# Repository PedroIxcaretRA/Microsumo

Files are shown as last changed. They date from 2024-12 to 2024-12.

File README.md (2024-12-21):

# Microsumo
Diseño, Programación y PCB para realizar un sumo clase 100gr (Microsumo)

## Tabla de Contenidos
1. [Descripción](#descripción)
2. [PCB](#pcb)
3. [Diseño](#diseño)
4. [Código](#código)

## Descripción
En el mundo de la robótica móvil, puede resultar un poco complicado encontrar información para desarrollar un prototipo en alguna de las diversas categorías existentes, como lo son sumo, seguidor de línea, robot de combate, drones autónomos, micromouse, entre otras. Si bien es posible encontrar cierta información de algunas categorías en repositorios de GitHub, videos de YouTube o artículos, esta puede estar en cualquier otro idioma, por lo que sea difícil su interpretación.

Por ello, en este repositorio, el objetivo es compartir todo lo aprendido en la categoría sumo, específicamente en la clase 100 gramos (micro). Esperamos que esta información sea completa y útil para tus proyectos, o al menos te brinde una idea clara de lo que implica esta categoría.

## PCB

En esta sección se comparte un Gerber perteneciente a una PCB realizada por nosotros. Al igual que se da el esquemático y una breve explicación para realizar una.

## Diseño

Se comparten archivos e ideas que hemos utilizado y algunas recomendaciones que podrían ser de ayuda.

## Código

En esta sección se comparte un código ejemplo y se da una breve explicación. 

Autores:
[MOCteam](https://www.instagram.com/mocteam17/)

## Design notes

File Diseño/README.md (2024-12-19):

# Diseño y Ensamble

El diseño del prototipo, al igual que el diseño de la PCB o la programación, evoluciona con el tiempo. Se prueba una cosa y otra, y aunque al principio puede que no se tenga un buen prototipo (o si), después de dos o tres competencias podrías identificar aspectos que necesiten cambios. Nuevas ideas y mejoras siempre surgen. Por eso, en esta parte del repositorio se presentará una idea general del diseño mecánico del robot, así como del ensamble del prototipo. Como en todo el repositorio, puedes seguir estos pasos al pie de la letra o adaptarlos según tus necesidades.

***Aunque dice "Diseño", y lo más probable es que se piense que aquí se enseñará a cómo diseñar un microsumo, la realidad es que con los archivos que se están compartiendo ya se puede tener una idea clara de cómo hacerlo. Por lo tanto, esta sección se centrará más en consejos prácticos y el ensamblaje del prototipo.***

## Tabla de Contenidos
1. [Descripción](#descripción)
2. [Base latón](#base-latón)
   - [Paredes](#paredes)
     - [Ensamblaje](#ensamblaje)
   - [Base sensores](#base-sensores)
4. [PLA](#pla)

## Descripción

El archivo base_microsumo_pro.rar contiene una base diseñada en SolidWorks (versión 2019), destinada a ser fabricada en latón. Puede ser enviada a maquilar en JLCPCB, PCBWAY, o cualquier otro lugar. Este archivo es totalmente modificable y lo puedes ajustar según tus necesidades.

No es fundamental usar una base de latón en un microsumo, versiones anteriores que se han realizado, el chasis del robot ha sido completamente de PLA con peso muerto (plomo), ha funcionado bastante bien, así que, si se prefiere usar PLA y plomo es una opción bastante viable, en el archivo Microsumo_v10.rar es una idea de lo que se usaba. Igual es totalmente modificable.

***Tip***
- El ángulo donde se coloca la navaja generalmente varía entre 20° y 30° de inclinación. Como recomendación, se sugiere usar un ángulo de 25°.

## Base latón

Una vez que se tiene la base de latón en proceso de fabricación o en su posesión, ya sea que se haya mandado a fabricar la opción presentada, modificado el diseño existente o incluso creado una propia, se procederá a diseñar el chasis del prototipo. 

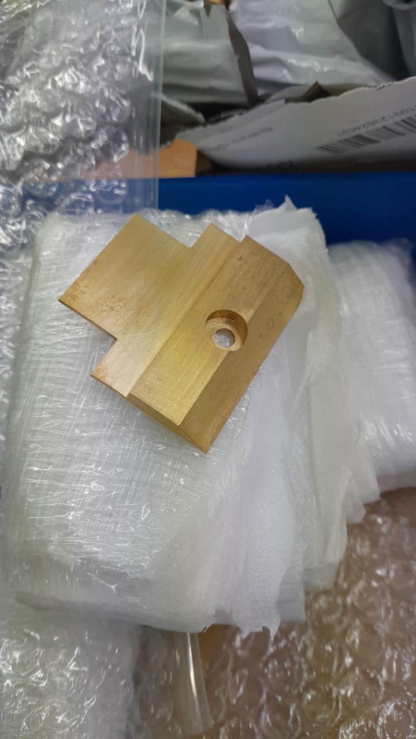
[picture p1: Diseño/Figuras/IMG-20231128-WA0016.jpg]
Baselaton


Para esto, se darán dos opciones que hemos utilizado, las cuales llamaremos *Paredes* y *Base Sensores*. 
- Paredes: Como su nombre lo indica, se tendrán las paredes laterales y trasera, fabricadas de PLA o cualquier otro filamento.
- Base Sensores: consiste en una pequeña base donde se colocaran los sensores y la tapa frontal, también fabricada de PLA.

En ambas opciones, la tapa frontal será construida de una herramienta conocida como [cuña](https://www.brochasexito.com.mx/productos/Accesorios/Cunas-Exito-de-Acero), esta herramienta se puede conseguir en COMEX (Mexico).

### Paredes

Se diseñará en la parte de arriba de la base algo como lo siguiente.

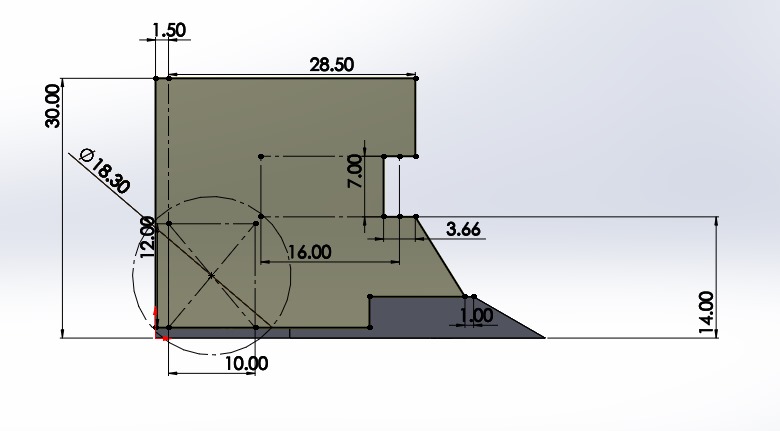
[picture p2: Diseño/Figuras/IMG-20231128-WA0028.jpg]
Paredes_moc


Las medidas dependerán de los sensores, batería(s), llantas y motores que se estén utilizando. En el ejemplo anterior se emplearon dos baterías de litio de 3.7V y 140mAh (RADOX), tres sensores de proximidad IR Pololu 38kHz de ganancia fija, dos micromotorreductores N20 de relación 30:1, un sensor QTR (de autoría propia), además de un par de rines y llantas.

Aunque se pueden hacer mejoras, por ejemplo:
- La tapa trasera podría reducirse a 1 mm o 0.5 mm.
- La medida de 28.5 mm podría ajustarse a 25 mm.
- La altura de 30 mm podría reducirse a 25 mm o 27 mm.

Estos cambios modificarían ciertas partes del diseño, pero consideramos que quedarían a la perfección. Es cuestión de experimentar con lo que se tiene y ajustar según las necesidades.

#### Ensamblaje

Se puede pintar la base o colocar una pegatina, ya sea en un acabado totalmente negro, brillante o mate o tipo fibra de carbono. Esto dependerá del gusto de cada persona.

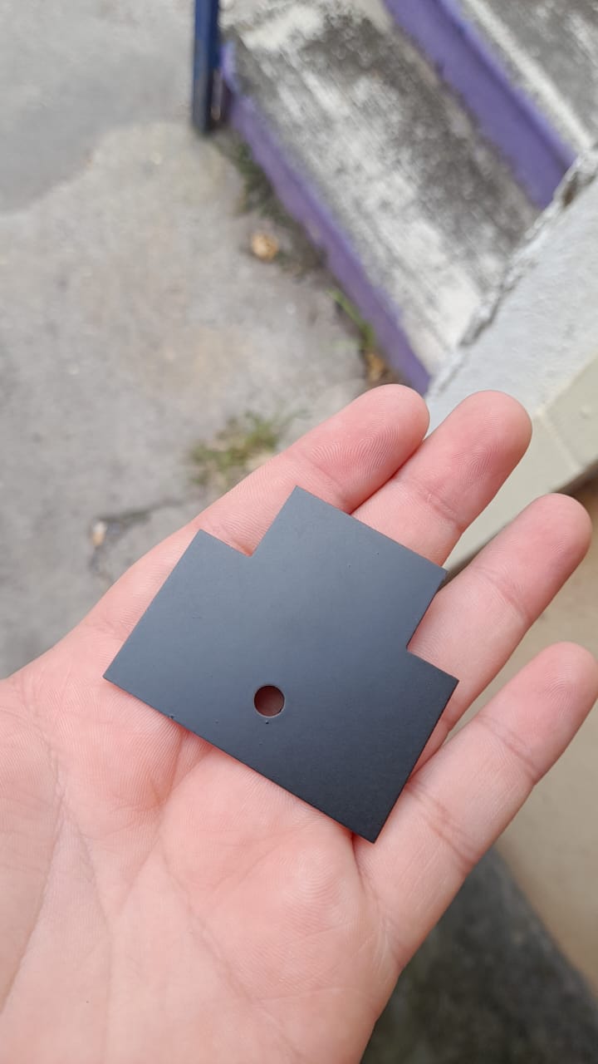
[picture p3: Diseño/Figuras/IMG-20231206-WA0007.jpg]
Basepint


Una vez que se tienen las impresiones en 3D de las paredes, estas se fijan a la base de latón utilizando Kola-Loka. Colóquese pared por pared, con calma, para tener un mejor resultado. El resultado final debería verse de la siguiente manera.

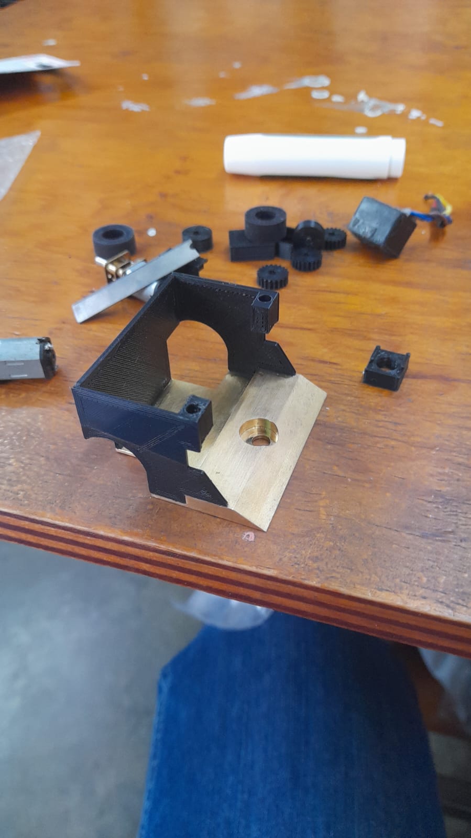
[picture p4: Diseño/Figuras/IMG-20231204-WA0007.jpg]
BasePar


A partir de aquí, el ensamblaje será el mismo si se utilizan motores N20 rectos, ya que existen diferentes modelos. ¿Qué significa que será el mismo? Justamente eso: sin importar cuál opción se utilice (Paredes o Base Sensores, con base de latón o PLA), la forma en la que se colocarán los motores y cómo se transmitirá la potencia será igual para todas las configuraciones. Por lo tanto, se explicará el proceso con el máximo detalle.

La idea es colocar los motores como se muestra en la figura de abajo. 
Para fijar los motores a la base, se utiliza Kola-Loka. Como sugerencia adicional, se podría agregar un poco de bicarbonato a la mezcla. Esto genera una sustancia más fuerte y resistente.

***Tip***

- Supondremos que ya se cuentan con las llantas. Una sugerencia importante que debes seguir al pie de la letra es no fijar los motores al 100%. Utiliza únicamente la cantidad necesaria de Kola-Loka para que los motores queden semifijos y no se muevan.
Una vez que estén semifijados, coloca las llantas y verifica que no haya desnivel utilizando un espejo (por el reverso del mismo). Es fundamental asegurarse de que la parte donde se colocará la navaja quede recargada de manera uniforme sobre la superficie. Esto para que cuando se coloque la navaja no se tenga un lado alzado.

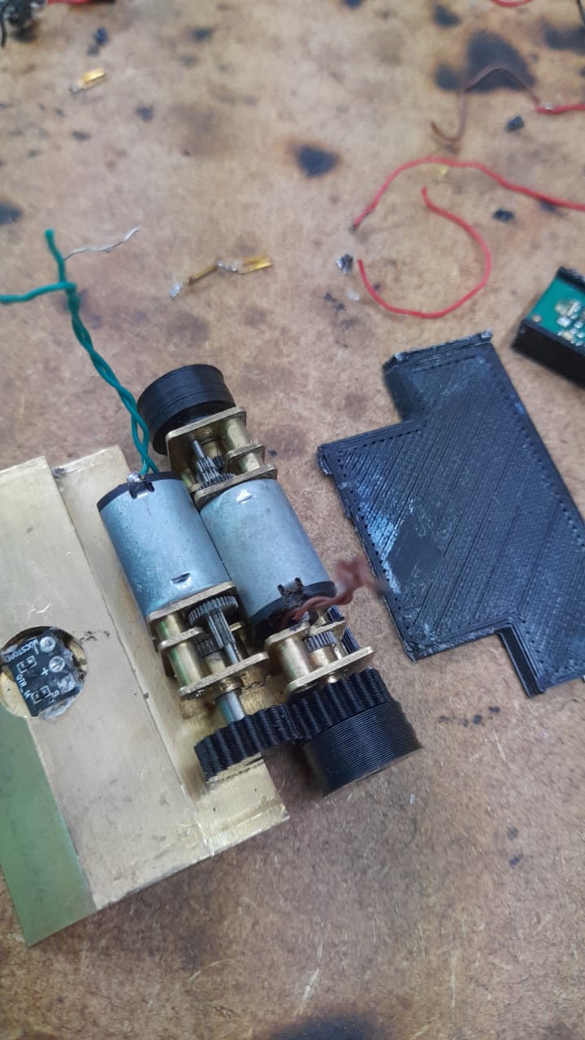
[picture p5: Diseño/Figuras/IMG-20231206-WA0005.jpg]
Motores


Para lograr esto, hay un aspecto que se debe observar con detalle: debido a las medidas, los motores no pueden colocarse de forma colineal. La solución consiste en configurar el sistema de la siguiente manera: se utilizan dos engranajes del mismo tamaño, lo que permite tener una relación 1:1. En esta configuración, un engranaje está conectado al eje del motor y el otro a una caja de reducción.

Existe otra forma de implementar esta configuración, que consiste en colocar un rodamiento en una pieza impresa en 3D y usar un eje de motor. Aunque esta opción resulta útil, en nuestra experiencia, no proporciona el resultado deseado. Por esta razón, se optó por utilizar una caja de reducción de los mismos motores, pero únicamente la última parte, que es la encargada de sostener el eje. Esta solución resulta bastante práctica y funcional.

En las tres figuras de abajo muestran ejemplos del sistema con rodamiento.

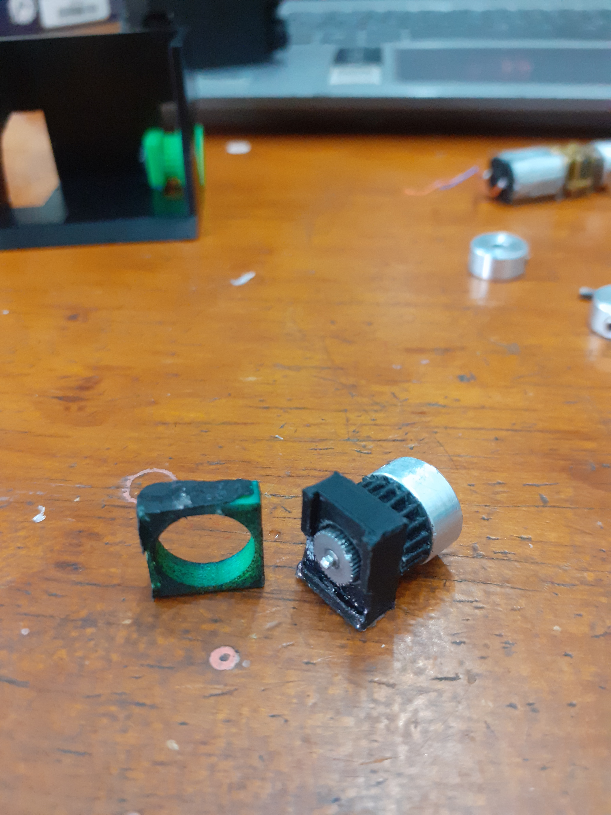
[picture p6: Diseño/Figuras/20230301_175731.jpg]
Motores1


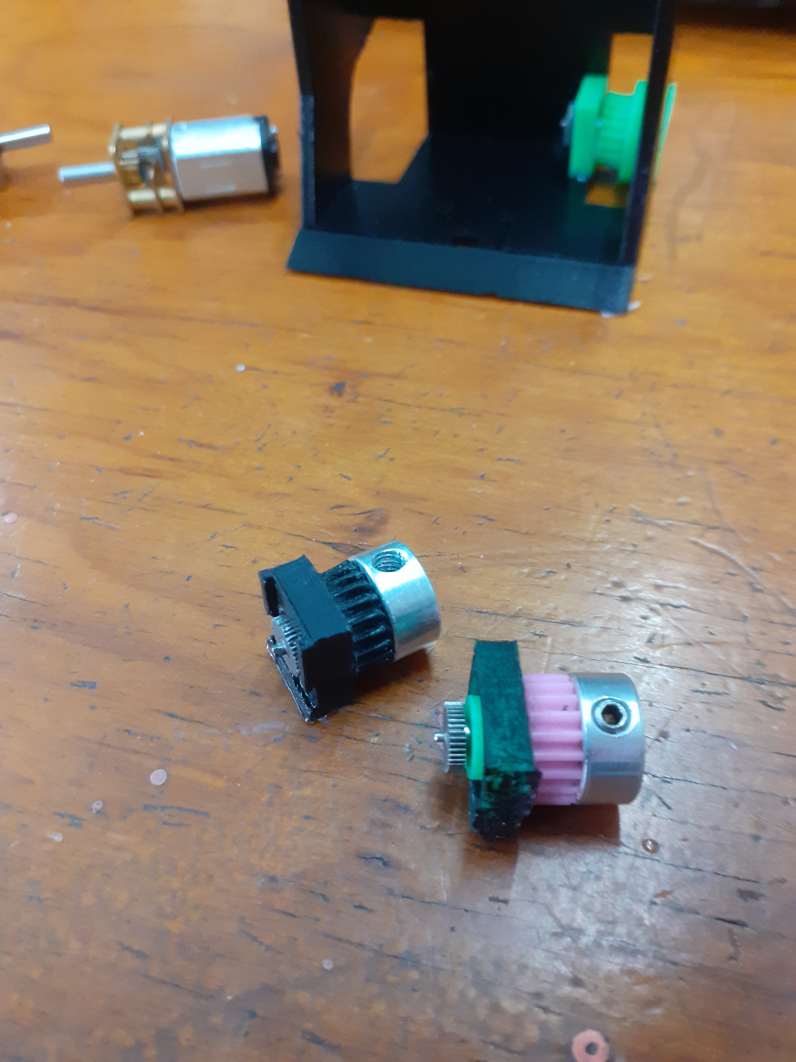
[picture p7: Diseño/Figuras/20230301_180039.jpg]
Motores2


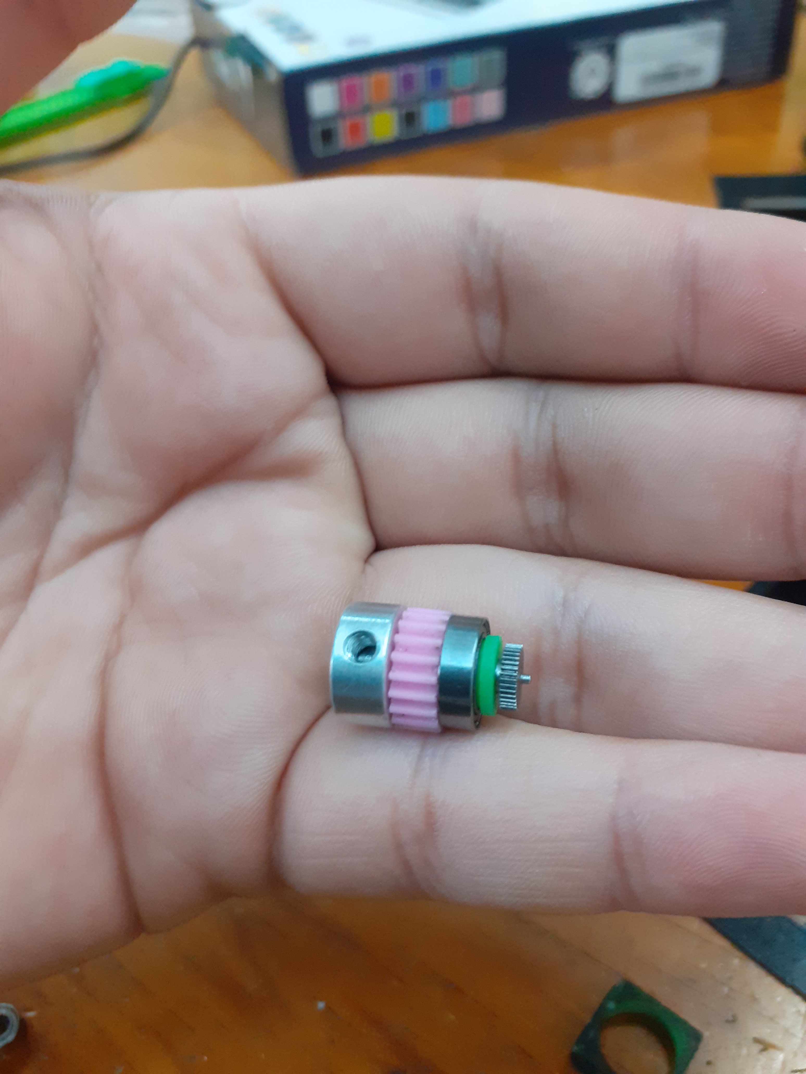
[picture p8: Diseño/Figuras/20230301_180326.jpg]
Motores3


***Tip***

- Los rines y engranes pueden fabricarse en PLA. Personalmente, solemos utilizar rines de aluminio y engranajes de PLA. Sin embargo, en AliExpress hemos encontrado engranajes de latón, que podrían resultar bastante útiles dependiendo de la aplicación.

- En cuanto a las llantas, aquí en México las conseguimos a través de compañeros de otros equipos que las venden. Parece que siempre es un reto conseguir esas llantitas.

Para este punto, ya se deben de tener fijadas las paredes y los motores, asegurándose de que no haya ningún desnivel. A continuación, se procederá con la colocación de los sensores, las baterías y la PCB.

Baterías:

 - Primero, coloca las baterías en la parte trasera. Estas se pueden acomodar según las necesidades del diseño o el espacio disponible.

Sensores:

 - Coloca el sensor de piso utilizando un poco de silicona para fijarlo en su lugar.

 - Luego, instala los sensores IR. Aquí, el proceso dependerá del modelo de sensores que estés utilizando.

Nota sobre los sensores:

 - Los sensores más recomendables son los RZ60S de Sumozade, una empresa turca. Debido a sus dimensiones, son ideales para este tipo de robots. Si no es posible conseguirlos o no están disponibles al momento de ensamblar el prototipo, otras opciones viables son los JS40F de Jsumo (también turca) o los sensores Pololu mencionados anteriormente. O bien cualquier tipo de sensor con los que cuentes.

En este caso, se utilizaron sensores Pololu, lo que permitió que el prototipo adquiriera la siguiente forma a medida que avanzaba el ensamblaje.

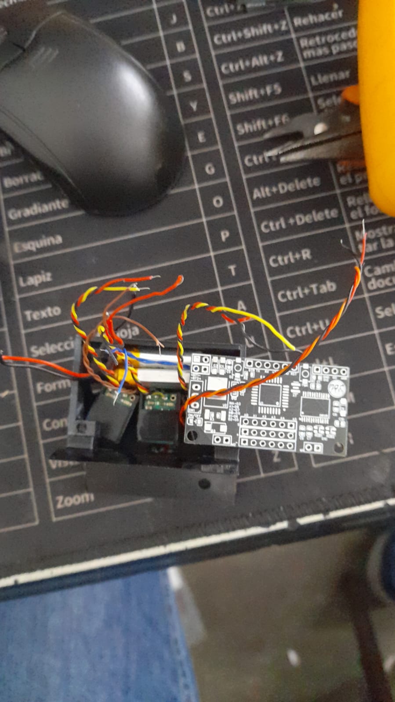
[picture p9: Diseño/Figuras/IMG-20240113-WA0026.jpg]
S,P,B


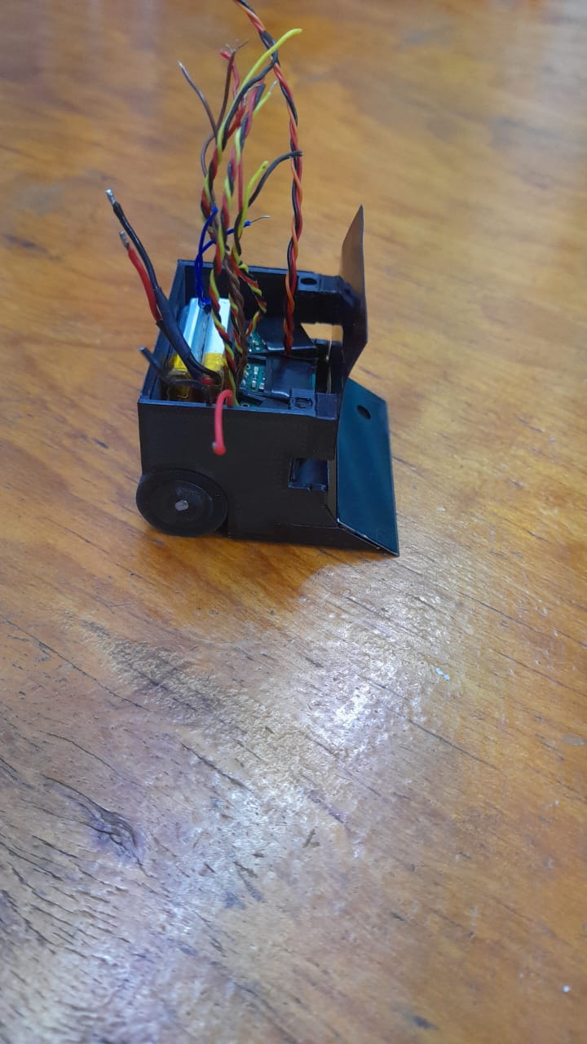
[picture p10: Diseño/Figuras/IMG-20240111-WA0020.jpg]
SPB2


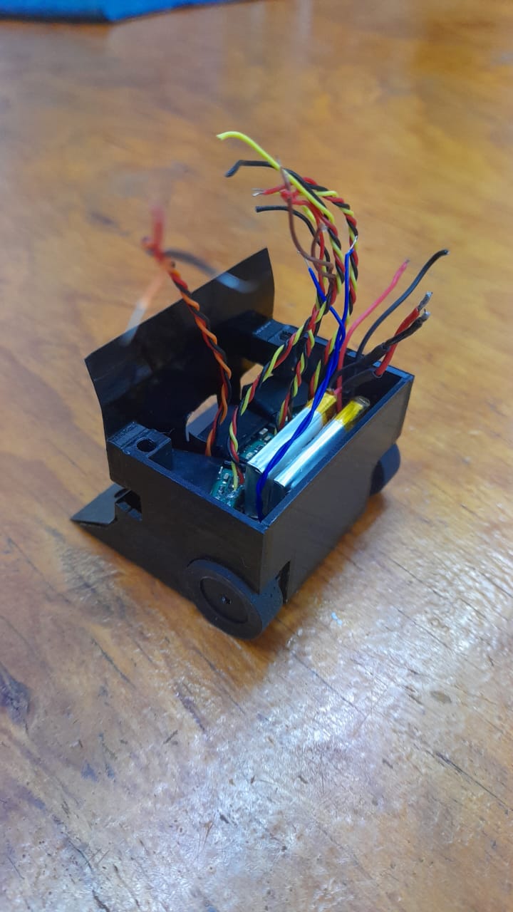
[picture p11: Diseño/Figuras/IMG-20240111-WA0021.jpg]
SPB3


Si se utilizan sensores Pololu, aquí van algunos consejos útiles:

1. Diseñar una carcasa específica para los sensores:
   - Fija los sensores a la carcasa con silicona en la parte trasera. Esto no solo asegurará que los sensores queden firmes en su lugar, sino que también ayudará a proteger los cables soldados, evitando que se desprendan o se dañen.

3. Colocar cinta aislante en la parte superior:
   - Esto es importante debido a los emisores del sensor, ya que la cinta ayudará a reducir interferencias o lecturas erráticas.

4. Considerar una carcasa alternativa:
   - Si el diseño inicial no es suficiente o no se ajusta a tus necesidades, puedes optar por diseñar una carcasa diferente que se adapte mejor al prototipo.

5. Características del sensor Pololu:
   - Pin de enable: Permite habilitar o deshabilitar el emisor del sensor según sea necesario.
   - Potenciómetro (pot): Facilita la regulación de la distancia de detección. Generalmente a la mitad.

PCB:
 
 - La PCB se fija a las paredes colocando un tornillo M3, se puede colocar un inserto en las paredes para que después se coloque el tornillo.

En este paso, se coloca la PCB y, posteriormente, se sueldan los cables de los motores y sensores. Es importante soldar las baterías primero, ya que su posición puede dificultar la soldadura una vez que la PCB esté colocada. Alternativamente, puedes soldar todo el cableado antes de fijar la PCB para mayor comodidad. 

Tapa frontal:

 - La tapa frontal puede cortarse con la ayuda de un esmeril angular 4" (o como lo conozcas) y, utilizando un Dremel, se realiza el corte en la sección destinada para los sensores.

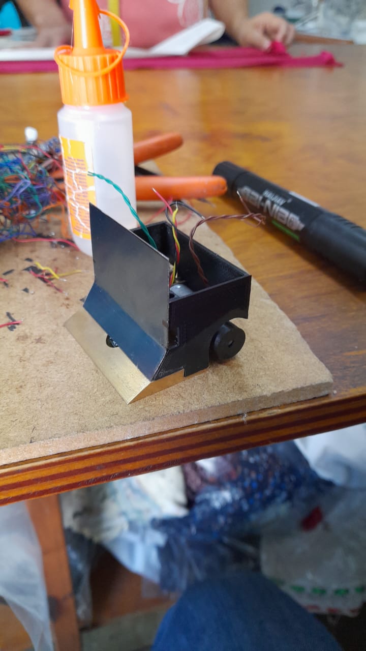
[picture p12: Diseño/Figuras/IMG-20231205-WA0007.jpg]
tapacor


 - Se presenta la tapa y se enciende el robot para verificar que los sensores no presenten problemas de interferencia con esta. Se sugiere pintar la tapa de negro por ambos lados para evitar reflejos o interferencias ópticas.

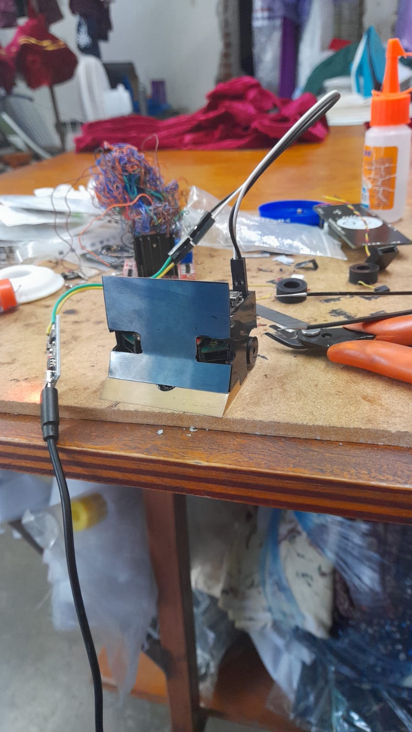
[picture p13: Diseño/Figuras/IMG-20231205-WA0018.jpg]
tapacor2


La tapa se fija a las paredes, usando Kola-Loka.

Ya se han colocado las paredes, motores, sensores, baterías, tapa y llantas; lo único que resta es colocar la navaja.

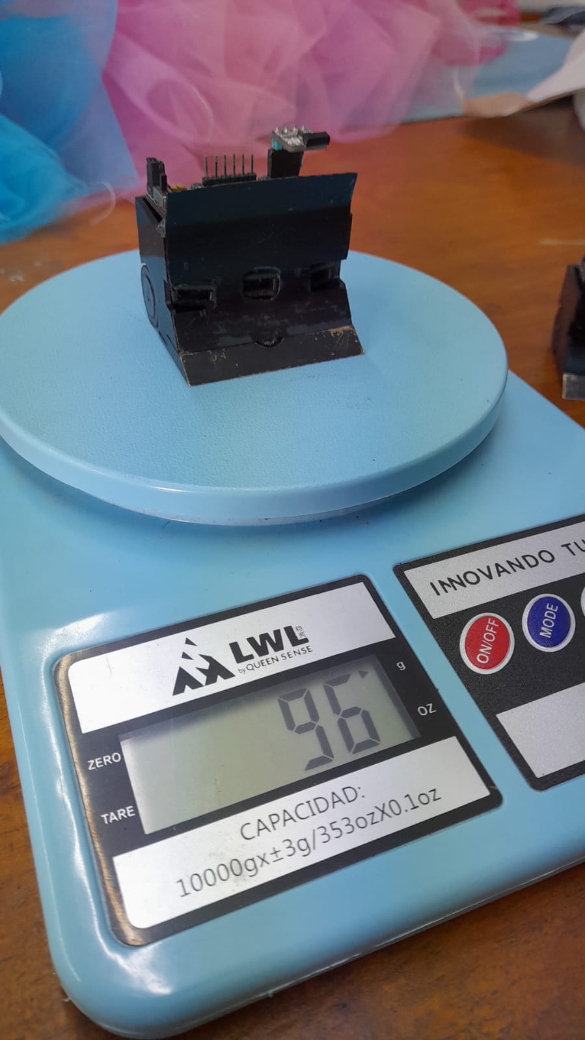
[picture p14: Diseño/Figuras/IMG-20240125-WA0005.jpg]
Montado


Es importante elegir el tipo de navaja adecuado. En las primeras versiones del prototipo, utilizábamos navajas de cúter pequeño, las cuales se cortaban a la medida de 50 mm. Más adelante, un compañero de competencia me regaló una navaja Kanzawa de 50 mm. Desde entonces, hemos utilizado este tipo de navajas, que son de origen japonés y un poco complicadas de conseguir, pero no imposible.

Existen otras opciones, pero como con todo lo mencionado en este repositorio, dependerá del ingenio y creatividad que se apliquen al proyecto.

Para colocar la navaja a la base se utiliza cinta doble cara. Hay en el mercado bastante opciones, aqui dare dos opciones, cinta que se consigue en [Walmart Cinta de Montaje Ceys Montack Doble Cara Rojo](https://super.walmart.com.mx/ip/cinta-de-montaje-ceys-montack-doble-cara-rojo-2-5-m/00841151977240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) y en Aliexpress [Cinta de doble cara súper fuerte de 5M](https://es.aliexpress.com/item/1005006277925414.html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).

En la figura de abajo se pueden observar tres diferentes tipos de navajas utilizadas: Navaja cortada, Kanzawa cortada, Kanzawa de 50mm. 

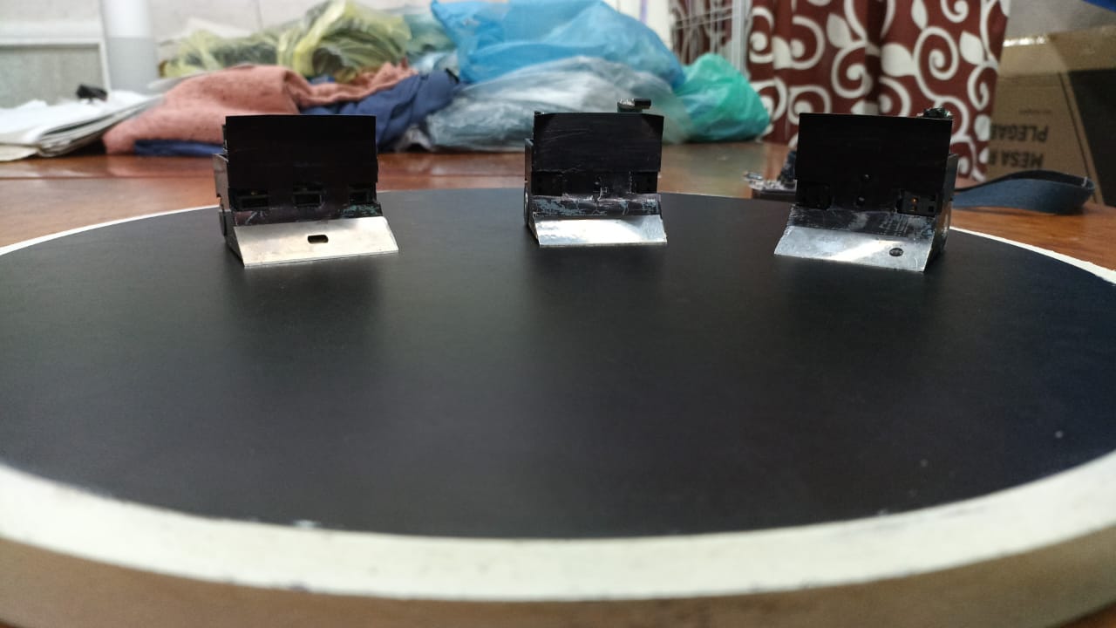
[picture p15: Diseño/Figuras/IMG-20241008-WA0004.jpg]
Navajas


***Tip***

- Número de sensores: Este número puede variar dependiendo del gusto o las necesidades del diseño. Usualmente, hemos utilizado de 3 a 4 sensores: uno para el piso y tres(dos) para la detección del oponente. La colocación también depende de lo que desees lograr. Puedes optar por poner uno que mire hacia enfrente y dos en los laterales, de forma que los emisores sean visibles pero los receptores no. O bien, puedes poner los receptores visibles y los emisores ocultos.
- Colocación de la navaja: Para colocar la navaja, coloca un poco de cinta en la parte de la navaja, usando no más de la mitad de la superficie. Luego, pégala a la base. Con un espejo, coloca el robot encima y observa desde atrás para verificar que no entre luz, lo cual indicaría que la navaja está calibrada correctamente. Mueve el robot un poco para asegurarte de que la navaja no raspe el suelo. Después de cada combate, revisa que la navaja siga bien colocada. Si no es así, simplemente empuja la navaja hacia abajo desde el lado donde entra luz.  ***Este proceso requiere bastante practica y se va a ir mejorando con el paso de las competencias***
- Añadir peso al frente: Si lo consideras necesario, puedes añadir peso al frente del robot. Lo ideal es llevar al robot a su límite máximo de peso, que debería estar entre 98 y 100 gramos como máximo. ~~Una mala práctica es llevar el robot al límite, que se homologué sin arrancador y cuando se coloque el arrancador te dé un peso de 101 -102 gr. Pareciera poco, pero se nota la diferencia de peso~~.

El resultado final que deberías de tener es algo como lo siguiente.

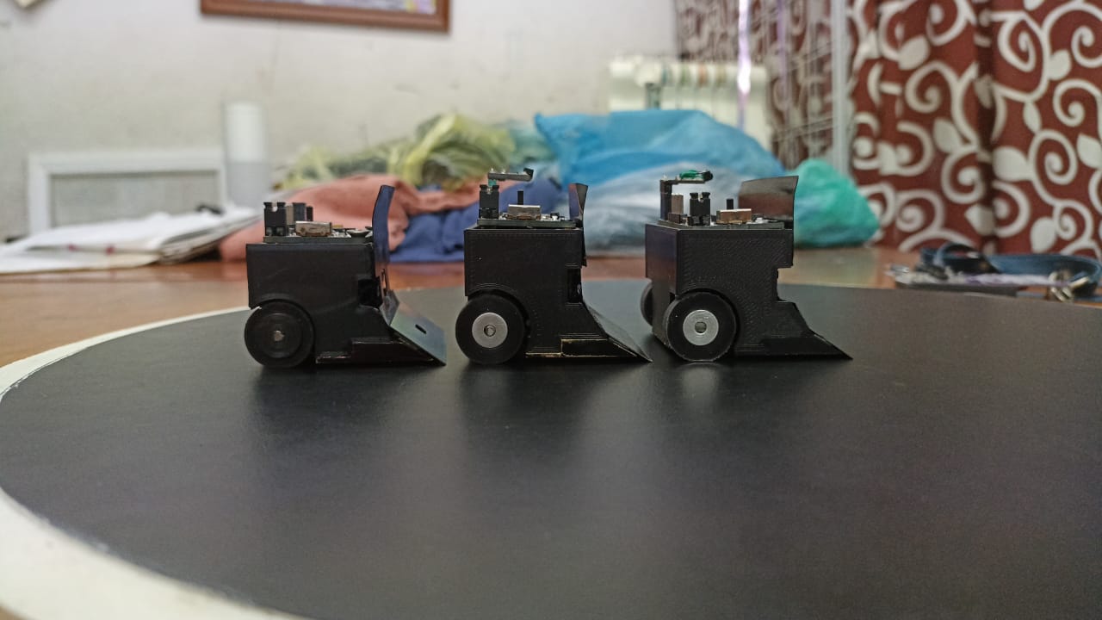
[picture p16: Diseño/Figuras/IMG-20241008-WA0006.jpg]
B,B,Y


Los mismos robots pero en un angulo diferente.

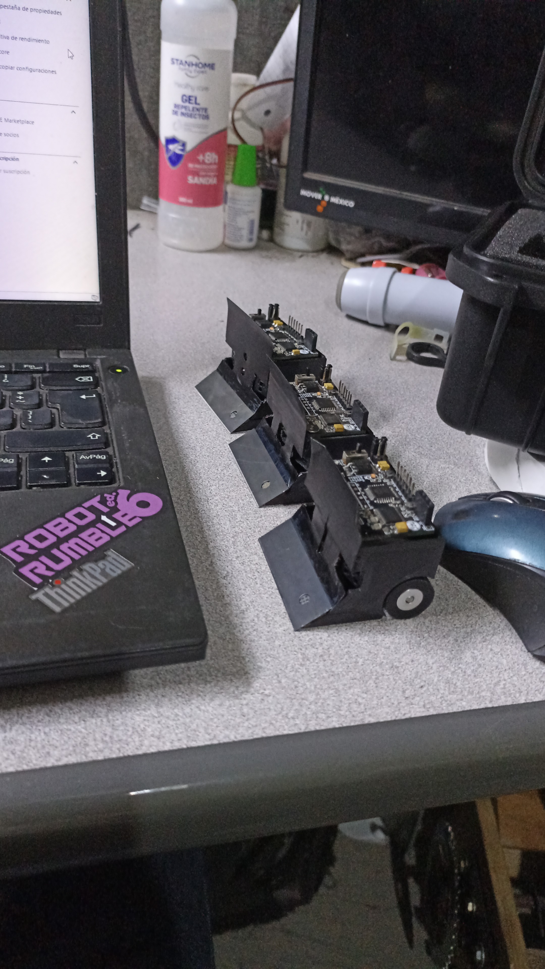
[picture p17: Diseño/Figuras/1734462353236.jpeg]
Y,B,B


### Base Sensores

Para este diseño, la idea principal es sencilla: concentrar el mayor peso en la parte delantera del robot. Esto se logra mediante las siguientes modificaciones:

- Quitar las paredes laterales: Eliminando el peso innecesario de las paredes laterales, se puede redistribuir el peso hacia la parte frontal.
- Reducir la pared trasera: Disminuyendo su tamaño o grosor, se aligera la parte trasera.
- Utilizar baterías más pequeñas: Un par de baterías de menor tamaño permitirá liberar espacio y peso, las beterías pueden ser del mismo amperaje, pero con diferentes dimensiones.

Con estas optimizaciones, el peso liberado puede ser utilizado para añadir materiales como latón, plomo, u otros elementos pesados en la parte frontal del robot, actuando como peso muerto.

El resultado sería un diseño como el que se ilustra en la siguiente figura.

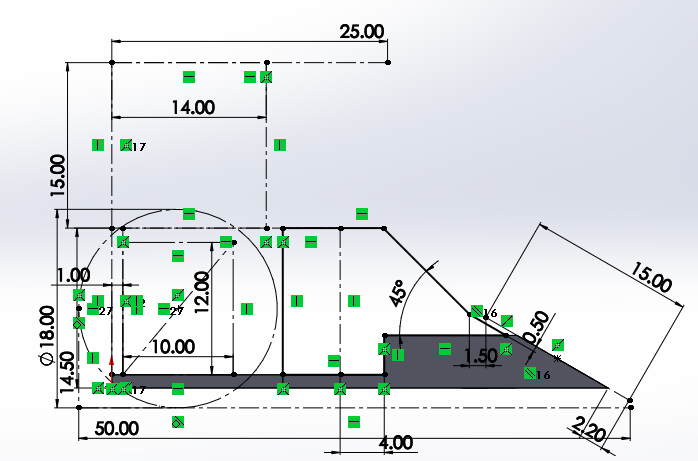
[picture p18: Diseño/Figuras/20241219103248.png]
BS


Una vez que se tiene la pieza impresa en 3D y la tapa trasera de aproximadamente de un grosor de 0.5 mm, se procede con los siguientes pasos ya antes explicados:

- Montar las piezas en la base de latón: Ambas partes deben fijarse con Kola-Loka
- Colocar los componentes: Sigue el procedimiento explicado anteriormente para instalar los motores, sensores, baterías y la tapa delantera. Recuerda revisar que todo esté correctamente alineado y ajustado, sin interferencias entre los componentes.

  ***Tip**
  - Usa baterías de mínimo 100mah ya que hemos probado con baterías de 80mah y estas han fallado a la hora de estar en combate.
  - Puedes rediseñar la tapa delantera, modificar la colocación de los motores e incluso ocupar las mismas baterías.

Al finalizar, deberías tener un prototipo ensamblado similar al que se muestra en las siguientes imágenes, con una distribución de peso optimizada.

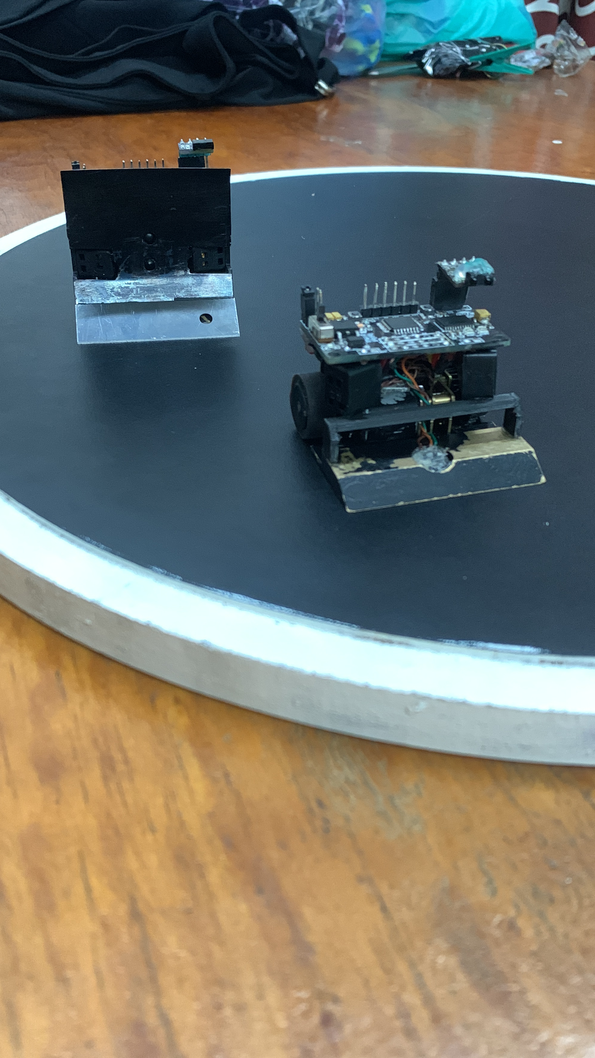
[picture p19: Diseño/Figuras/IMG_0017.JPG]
BSM


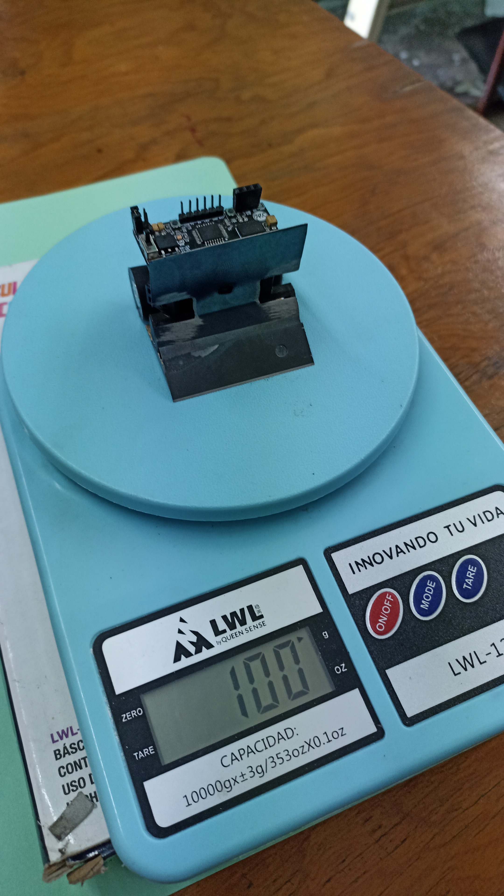
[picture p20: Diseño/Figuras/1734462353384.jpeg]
BSM2


Si jugaste bien con las medidas a la hora de diseñar, la PCB se podrá fijar con cinta doble cara a los sensores (depende de los sensores que se ocupen).

**Nota:** En la segunda figura se puede observar que el robot está al límite y aún no cuenta con el arrancador, por lo que se le tendría que quitar un poco de peso muerto para que, a la hora de colocar el arrancador, este no tenga problemas de homologación.

Hasta aquí se presenta la opción utilizando una base de latón. Puedes modificar la base de latón, haciéndola un poco más pequeña y con mayor peso adelante, de manera que solo sea necesario colocar los sensores y demás componentes. También existe la posibilidad de no usar una base de latón y, en su lugar, combinar la idea de Base Sensores con la siguiente opción que se presentará. Todo dependerá del gusto y lo que se necesite.

## PLA

En esta sección seremos breve, ya que el proceso de colocar los motores, elegir los sensores, seleccionar la navaja y fabricar la tapa frontal ya ha sido explicado. Por lo tanto, solo se presentará una explicación breve con algunas ideas sobre por qué realizarlo de esta manera.

Puede presentarse el caso de que no se cuente con los recursos necesarios para obtener una base de latón. En este caso, una buena alternativa es diseñar un chasis de PLA y añadir plomo como peso muerto. Esta opción, en nuestra opinión, ofrece un mayor margen para implementar ideas creativas.

En el archivo microsumo_v10 se encuentra el diseño del último microsumo que uno del equipo realizó utilizando esta metodología. En ese entonces, usaba una batería Tattu de 7.4V 300mAh, sensores Pololu y aluminio como peso muerto, ya que no disponía de plomo. A decir verdad, este diseño le permitió obtener algunas victorias y alcanzar uno que otro podio en competencias.

Sin embargo, siempre hay margen para mejorar. Por ejemplo, modificar completamente el chasis para utilizar baterías individuales, lo que ahorra espacio; emplear sensores RZ60S o continuar con Pololu; reducir las paredes del chasis; y agregar plomo en la parte delantera. Con estos ajustes, el diseño sería más eficiente, ya que un compañero del equipo utiliza esta idea y le ha dado excelentes resultados.

La idea es como la siguiente, tener el chasis de PLA y colocar plomo:

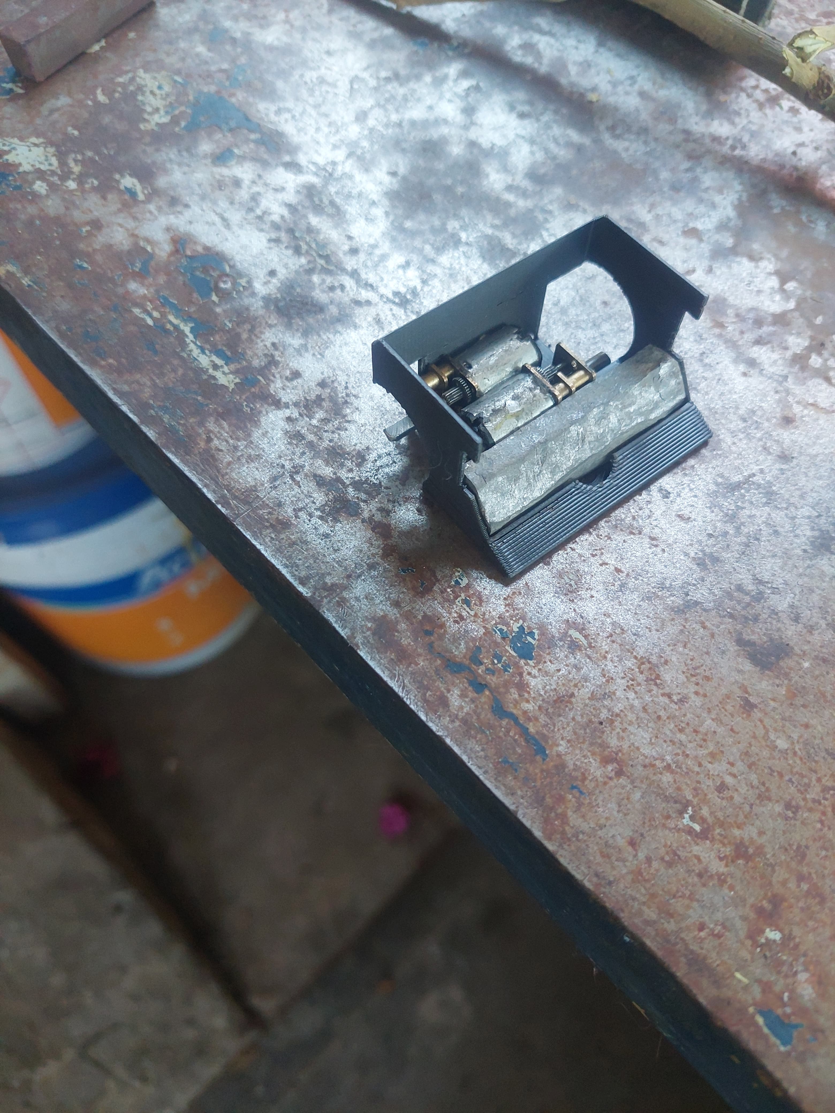
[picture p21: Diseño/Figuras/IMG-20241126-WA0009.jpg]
PLA5


El demás ensamblaje seria el mismo.

En las siguientes dos figuras se muestran ideas de prototipos que fueron desarrollados, actualmente estas ideas están retiradas, pero pueden ser de ayuda como referencia y entendimiento de la opción presentada.

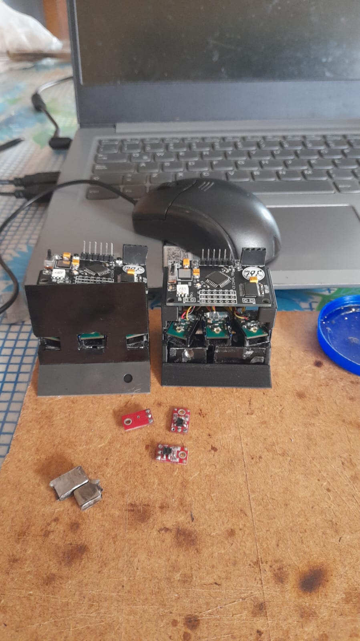
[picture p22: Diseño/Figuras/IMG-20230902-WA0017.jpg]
PLA1


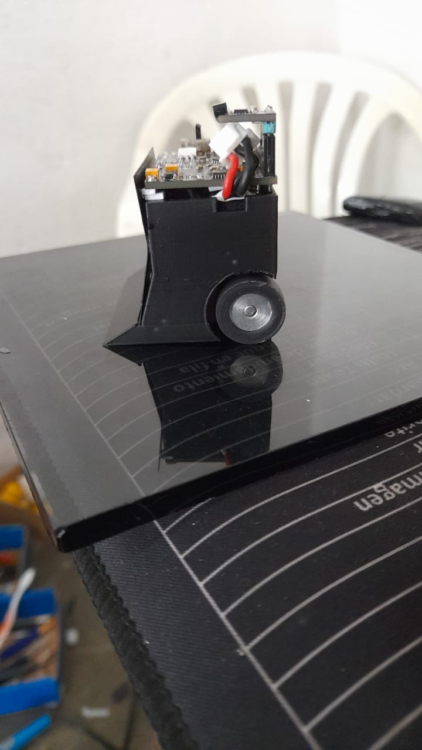
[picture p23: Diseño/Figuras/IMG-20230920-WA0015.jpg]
PLA2


En la siguiente figura se muestra la idea actual desarrollada por un compañero.

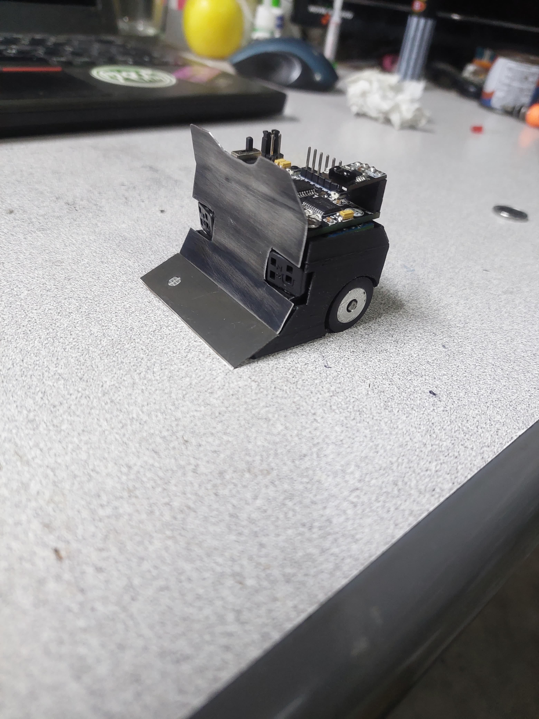
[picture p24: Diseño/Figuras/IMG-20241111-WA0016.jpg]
PLA6


Como se puede observar se dio una explicación lo más clara posible, si surgiera alguna duda puedes contactar con los autores de este repositorio, esperamos que todo esto te ayude en el diseño de tu prototipo.

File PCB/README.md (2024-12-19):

# PCB
Obtener una PCB funcional para cualquier prototipo que se este desarrollando puede ser una tarea significativa, ya que requiere tiempo, investigación y numerosas pruebas. Estar seguro de que el prototipo que se tiene será el último antes de mandarlo a fabricar es crucial. Es por eso que en esta sección del repositorio, te compartimos una opción viable que se podría considerar a la hora de realizar un microsumo.

## Tabla de Contenidos
1. [Descripción](#descripción)
2. [Esquemático](#esquemático)
3. [PCB MOCteam](#pcb-mocteam)
   1. [PINOUT](#pinout)

## Descripción
Como se mencionó anteriormente, esta es una tarea significativa. Si logras encontrar una PCB comercial, el proceso será mucho más sencillo, ya que alguien más habrá realizado este trabajo por ti.

En caso de que no se tenga acceso a una, aquí te compartimos una PCB diseñada específicamente para este propósito. Sus dimensiones son 45 mm x 25 mm, lo que la hace perfecta para las especificaciones de un 
microsumo. Esta PCB fue diseñada en EasyEDA, y puedes cargar el archivo Gerber en el servicio de JLCPCB para su fabricación.

Es muy posible que cuando encuentres este repositorio, ya sea por un video, una investigación o cualquier otro medio, no se tenga el acceso a los componentes necesarios. Por ello, se incluye una sección del esquemático para que se pueda replicar la PCB.

Si se es nuevo en este mundo, lo más probable es que debas investigar y buscar los componentes que utilizarás. Aunque no es un proceso complicado, puede resultar algo tedioso. La recomendación es que utilices componentes con medidas 0603, ya que tienen un tamaño ideal para soldar con cautín, en caso de que no cuentes con una estación de soldadura.

En cuanto a proveedores, se sugiere LCSC Electronics, que forma parte de JLCPCB, o también Aliexpress como alternativa.

Si no se tiene la experiencia soldando PCBs, se recomienda tomarlo con calma y tener paciencia. Soldar requiere práctica, pero es algo que se puede aprender desde cero. Personalmente, todas las PCBs que hemos ensamblado, han sido utlizando únicamente un cautín. 

Por ultimo, la placa tiene como mCU un Atmega328p-au por lo que se puede programar usando el IDE de Arduino. En la sección de PCB MOCteam se explica como cargar un programa usando un Arduino nano.

**Nota: Si se usa cautín, se recomienda tener malla desoldadora de cobre.**

**Nota: El esquematico pdf y el gerber son diferentes pero es basicamente lo mismo**

## Esquemático

[***Los componentes se encuentran en el BOOM***](BOM_Microsumo_30_11_2024_2024-12-15.csv)

[***Archivo completo en el PDF Schematic_Microsumo***](Schematic_Microsumo_30_11_2024_2024-12-15.pdf)

En la primera parte, se encuentran dos headers que servirán para la conexión de las baterías (batería de Li-ion 3.7V a 140mAh) y el interruptor. Al momento de diseñar la PCB, se sugiere que estos headers estén lo más cerca posible, ya que se requiere un jumper para la suma de voltajes.

Conexión baterias

En la segunda parte, se encuentra el circuito de regulación de voltaje con un 7805. Esta sección incluye un LED que indicará cuando la PCB esté energizada.

Regulador

La tercera parte es un microcontrolador (mCU), el IC Atmega328p-au, con los componentes necesarios para que funcione de manera eficiente. Aquí es importante prestar atención, ya que, si se quiere o requiere añadir el pin de DTR, se debe colocar una conexión con un capacitor (0.1µF) entre el RPB y la resistencia de 10k, y la otra conexión al pin asociado al DTR. El SPB en el código estará configurado como PULLUP, por lo que está conectado de esta manera. Además, si se quiere habilitar el pin TX, se debe colocar un indicador que lo mande a ese pin (31).

mCU

En la cuarta parte se tiene el arrancador y el RGB. Se podría agregar otro RGB, solo se necesita habilitar el pin DI y conectarlo al DO del nuevo RGB; lo demás es igual. Si requiere agregar el pin RDY del arrancador, se puede asociar a un pin disponible del mCU.

Arr

La quinta parte corresponde a la alimentación y señal de los sensores. En P1 podría agregarse el pin TX y DTR, y es donde se programara la PCB.

Alimentación

La sexta y última parte corresponde al controlador de motores, que es el TB6612FNG, un componente bastante eficiente para controlar motores DC.

la_TB

[***Esquemático del Arduino pro mini***](https://www.arduino.cc/en/uploads/Main/Arduino-Pro-Mini-schematic.pdf)

## PCB MOCteam

Si has decidido en mandar a fabricar la opción que se presentó, aquí se explicará qué es y dónde se encuentran cada una de las entradas y salidas de la tarjeta.

Una vez fabricada y ensamblada, tendrás las PCBs tal como se muestra a continuación, ya con todos los componentes soldados. Si observas, cada pin está identificado mediante serigrafía, lo que facilita saber a qué está asociado.

*En la figura de abajo no contiene componentes para una mejor compresión.*

PCB

En la etapa de regulación consiste en soldar dos baterías con dos header para poder cargarlas, se debe añadir un jumper en la parte externa de los headers. Además se tiene un regulador, un led como indicador, compontes pasivos y un diodo para protección de la tarjeta.

ERegulacion

Para cargar el programa a la PCB, se necesitara un Arduino Nano. Solo se utilizarán los pines RST, GND y RX. Se conecta el Arduino Nano a la computadora y se carga el programa como se haría normalmente. Durante el proceso, el LED asociado al pin 13 de cada placa parpadeara, y cuando en el IDE de Arduino aparezca el mensaje de que la carga ha finalizado, el proceso habrá concluido.

CP

**Nota: Si no se carga el programa, puede ser debido a que el mCU no tiene el [bootloader](https://tutoriales.rantec.mx/manual-para-cargar-bootloader-en-arduino/), en cuyo caso se tendrá que quemar. También puede ser que el resonador no esté bien soldado.**

### PINOUT

No hay mucho que agregar sobre el Pinout, ya que está serigrafiado, lo que facilita identificar a qué pin está asociado cada componente. Sin embargo, a continuación se detallan algunos puntos clave por si surge alguna duda:

- Recuadro color rosa: Contiene un botón pulsador (PBS) de propósito general, el cual está asociado al pin D2.
- Recuadro color amarillo: Incluye un LED conectado al pin D13.
- Recuadro color rojo: Está asociado a los pines que se conectan directamente al controlador de motores.
- Recuadro color naranja: Corresponde a los pines de entrada para los sensores. Aunque comúnmente se utilizan como pines analógicos, también pueden configurarse como entradas digitales, es decir, tienen - - -- funcionalidad dual. Los pines asociados son D14, D15, D16, D17, D18 y D19.
- Recuadro color morado: Contiene los LEDs RGB, que funcionan con un único pin de control, el D10.
- Recuadro color azul: Corresponde al arrancador, asociado al pin D12.

PINOUT

Al final de toda esta explicación la PCB debería verse de la siguiente manera. 

PCBfinal

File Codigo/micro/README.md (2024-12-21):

# Código

Existen muchas formas de programar, algunas más eficientes que otras, o que utilizan más o menos recursos. El código que se presenta en esta sección tiene como objetivo servir de referencia al momento de crear uno propio. Se asumirá que el lector cuenta con conocimientos previos de programación, por lo que se proporcionará una explicación breve del código para facilitar su comprensión y posible adaptación.

**Nota:**

- Si estás utilizando la PCB presentada y cargas el código tal cual está, respetando los pines donde se conectan los sensores, el código debería funcionar sin problemas. Es posible que los motores estén invertidos, pero esto sería cuestión de soldar y cambiarlos.

- El proceso de carga del programa se explica en la sección de PCB.

- Si deseas probar sensor por sensor y los motores, te dejo tres archivos de prueba. Además, puedes crear tus propios archivos si lo deseas.

- La libreria de FASTLED te tocara buscarla, y experienta con ella para modificar los colores.

## Tabla de contenidos

1. [Declaración](#declaración)
2. [void setup](#void-setup)
3. [void loop](#void-loop)
4. [void floor_move](#void-floor_move)
5. [void conditions](#void-conditions)
6. [void read](#void-read)
7. [void atacar](#void-atacar)
8. [void one](#void-one)
9. [void move](#void-move)
10. [Motores](#motores)

## Declaración

Se incluye la librería FastLED para configurar y controlar los dos LEDs RGB que se encuentran en la PCB. Se define el número de LEDs, en este caso 2 RGB, y el número del pin que transmite los datos (D10). Por último, se declara el arreglo CRGB leds[] con el número de LEDs a utilizar.

RGB

Se declaran los pines de la TB. Los pines están serigrafiados en la PCB.

TB

Se declaran los pines donde están conectados los sensores, el botón pulsador y el arrancador.

Pines

Se declaran las variables necesarias para conocer el estado de los sensores, el botón y el arrancador.

Pines

Por último, se declara el pin del LED y las variables auxiliares que se ocuparán en el resto del código.

Pines

## void setup

No hay mucho que explicar, más que se realiza una modificación al prescaler en la primera sentencia, lo que permite ajustar la frecuencia del temporizador. Posteriormente, se inicializan y configuran los LEDs RGB utilizando la librería FastLED.

Setup

## void loop

Se estará leyendo el estado del arrancador. Mientras su estado sea 0 (estado bajo), se leerá el estado del pulsador. Si el pulsador es presionado, se realizará una sumatoria en cada pulsación, y se encenderá el LED. Cuando el estado del arrancador sea 1 (estado alto), se llamará a la función floor_move(). Si el arrancador vuelve a un estado bajo, el ciclo se rompe, y todo se reinicia estableciendo los valores en 0.

Loop

## void floor_move

En esta función, se estarán leyendo los valores analógicos del sensor de línea. Si el valor leído es menor o igual a 60, se llamará a la función move(), lo que indica que se detectó la línea blanca. Si el valor supera este umbral, se llamará a la función conditions(count), pasando como parámetro el conteo de las pulsaciones del botón.

fm

## void conditions

En la función, si el parámetro no está dentro de los casos definidos en el switch-case, será enviado al caso default, y se llamará a la función atacar(). Si la pulsación es 1 o corresponde a alguno de los casos definidos, se ejecutará el código correspondiente a esos casos.

fm

## void read

Esta función es la más grande del código. Primero, lee los estados de los sensores. Luego, se encuentra un arreglo de condiciones if-else para cada sensor, asignándole un valor a una variable byte. Posteriormente, se realiza una sumatoria de estas variables byte y el resultado se guarda en otra variable byte, que contiene los valores combinados de los sensores. Esta variable se utiliza como parámetro en el switch-case. Dependiendo de la lectura, una variable pos tomará un valor específico, al igual que los LEDs. En la última parte del código se tiene un arreglo de sentencias if que guarda, por un breve periodo, la última posición del sensor que detectó. Por ejemplo, si fue el derecho el último en detectar, el valor correspondiente a "derecho" se guarda en la variable pos por medio segundo. Esto hace que el motor gire un poco más a la derecha. Obviamente, mientras el robot va girando y detecta la posición "izquierda", el motor se girará a la izquierda. Es bastante útil si se llega a perder la detección del robot oponente. Si no te funciona o covence lo podrias borrar y no habria problema. 

read

red2

read3

## void atacar

Se llama a la función read(), la cual retorna la variable pos. Esta variable servirá como parámetro para el switch-case, y dependiendo de su valor, se determinará cómo mover los motores.

atacar

## void one

No hay mucho más que decir, simplemente gira durante un tiempo y luego pasa a la función atacar.

one

## void move

Esta función sirve para mover el microsumo cuando detecta la línea blanca. Hay varias formas de hacer esto, a lo mejor no es la más eficiente, pero cumple su propósito.

move

## Motores

Por último, se tienen las funciones para la dirección de los motores. Existen dos tipos de "stop", y esto depende del tipo de driver que estés utilizando. En este caso, uno desenergiza los motores y el otro los manda a corto. Se sugiere revisar la hoja de datos del controlador que se esté utilizando.

motor

motor

Fue una explicación bastante breve pero esperamos que sea entendida y te sirva a la hora de realizar un prototipo de esta categoria.
Cualquier duda puedes contactar a los creadores de este repositoiro.

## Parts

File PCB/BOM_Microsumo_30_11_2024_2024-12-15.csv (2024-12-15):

ID | Name | Designator | Footprint | Quantity | Manufacturer Part | Manufacturer | Supplier | Supplier Part | Price | Pins | Contributor | JLCPCB Part Class | link
1 | Header-Female-2.54_1x6 | +,S | HDR-TH_6P-P2.54-V-F | 2 | 2.54-1*6P母 | BOOMELE(博穆精密) | LCSC | C40877 | 0.065 | 6 |  | Extended Part
2 | Header-Male-2.54_1x4 | ARR | HDR-TH_4P-P2.54-V-M | 1 | B-2100S04P-A110 | Ckmtw(灿科盟) | LCSC | C124378 | 0.038 | 4 | LCSC | Extended Part
3 | Header-Male-2.54_1x2 | BT1,BT2,M1,M2 | HDR-TH_2P-P2.54-V-M-1 | 4 | 826629-2 | TE Connectivity(泰科电子) | LCSC | C86471 | 0.376 | 2 |  | Extended Part
4 | 100nF | C2,C3,C4,C5,C10,C11 | C0603 | 6 | 0603B104K250NT | FH(风华) | LCSC | C694249 | 0.002 | 2 | LCSC | Extended Part
5 | 10uF | C6,C7,C9 | CAP-SMD_L3.2-W1.6-RD | 3 | CA45-A-16V-10uF-K | CEC(振华新云) | LCSC | C128254 | 0.062 | 2 | LCSC | Extended Part
6 | P2-0805UVTCS2-0.8T | D13 | LED0805-RD_PURPLE | 1 | P2-0805UVTCS2-0.8T | TUOZHAN(拓展光电) | LCSC | C2827270 | 0.014 | 2 | LCSC | Extended Part
7 | TB6612FNG(O,C,8,EL | DRVR1 | SSOP-24_L8.4-W5.8-P0.65-LS7.8-BL | 1 | TB6612FNG(O,C,8,EL | TOSHIBA(东芝) | LCSC | C88224 | 1.286 | 24 |  | Extended Part
8 | NCD0603B1-YJL | ON/OFF | LED0603-RD_BLUE | 1 | NCD0603B1-YJL | null | LCSC | C9900013174 |  | 2 | lcsc | Extended Part
9 | Header-Female-2.54_1x3 | P1 | HDR-TH_3P-P2.54-V-F | 1 | 2.54-1*3P母 | BOOMELE(博穆精密) | LCSC | C146243 | 0.054 | 3 |  | Extended Part
10 | 330Ω | R2,R4 | R0603 | 2 | SCR0603J330R | VO(翔胜) | LCSC | C3017748 | 0.001 | 2 | lcsc | Extended Part
11 | 10kΩ | R3 | R0603 | 1 | SCR0603J10K | VO(翔胜) | LCSC | C3017715 | 0.001 | 2 | lcsc | Extended Part
12 | WS2812C-2020-V1 | RGB1 | LED-SMD_4P-L2.0-W2.0-TL_WS2812B-2020 | 1 | WS2812C-2020-V1 | worldsemi | LCSC | C2976072 | 0.069 | 4 | lcsc | Extended Part
13 | SKRKAEE020 | RPB,SPB | SW-SMD_L3.9-W3.0-P4.45 | 2 | SKRKAEE020 | ALPSALPINE(阿尔卑斯阿尔派) | LCSC | C115357 | 0.103 | 2 |  | Extended Part
14 | SS12D00G4 | SW | SS12D00G4 | 1 |  |  |  |  |  | 3 | IIuIIa
15 | ATMEGA328P-AU | U1 | TQFP-32_L7.0-W7.0-P0.80-LS9.0-BL | 1 | ATMEGA328P-AU | MICROCHIP(美国微芯) | LCSC | C14877 | 2.131 | 32 |  | Extended Part
16 | L78M05CDT-TR | U3 | TO-252-3_L6.5-W5.8-P4.58-BL | 1 | L78M05CDT-TR | ST(意法半导体) | LCSC | C55509 | 0.084 | 3 |  | Extended Part
17 | 16MHz | X1 | OSC-SMD_3P-L3.2-W1.3-P0.95-L | 1 | CSTCE16M0V53-R0 | muRata(村田) | LCSC | C32180 | 0.251 | 3 |  | Extended Part

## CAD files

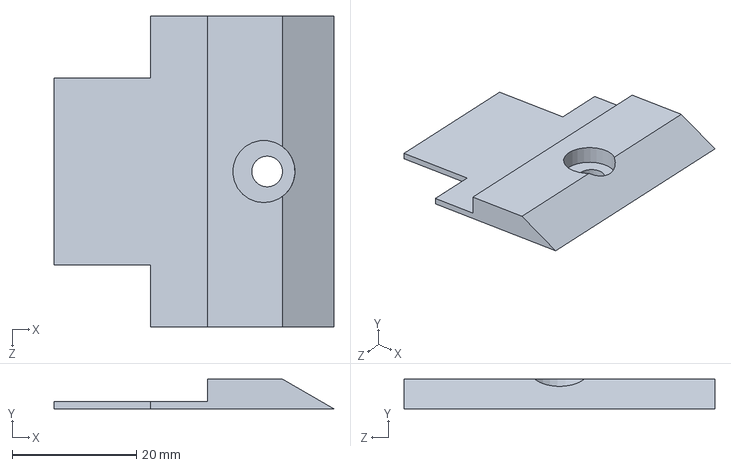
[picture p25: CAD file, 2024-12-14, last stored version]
Diseño/base_microsumo_pro.SLDPRT
45.0 x 4.77 x 50.0 mm

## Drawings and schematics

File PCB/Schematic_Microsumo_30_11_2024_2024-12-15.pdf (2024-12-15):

## GND

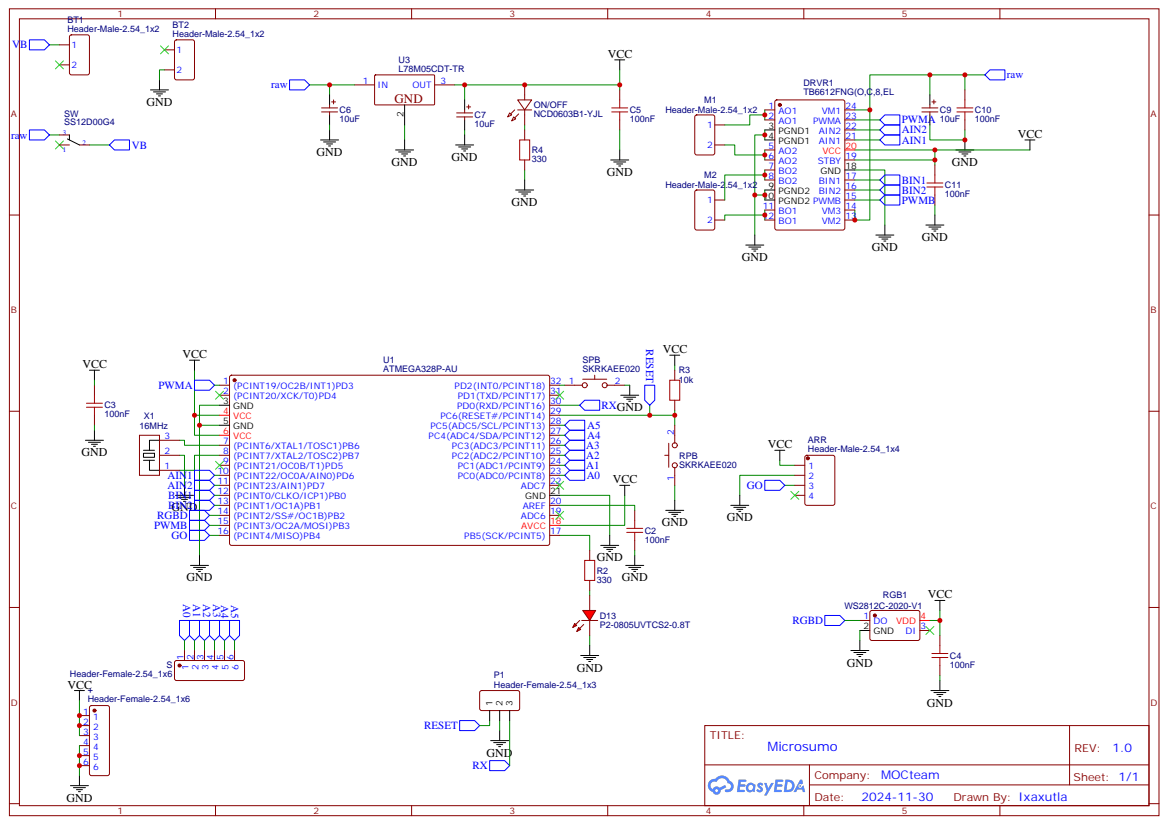
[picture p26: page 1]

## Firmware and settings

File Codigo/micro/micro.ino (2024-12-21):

//MOCTEAM-Micro
//rgb pins
#include <FastLED.h>
#define NUM_LEDS 2
#define DATA_PIN 10
CRGB leds[NUM_LEDS];
//TB pins
//-------right motor
#define in1 3
#define a1 8
#define a2 7
//-------left motor
#define in2 11
#define b1 6
#define b2 5
//sensors, push-button and start module
const int sr = 14;  //right
const int sm = 16;  //mid
const int sl = 15;  //left
const int sf = A3;  //line
const int pb = 2;
const int arr = 12;
//states of sensors, button and start module
int stsr;
int stsm;
int stsl;
int stsf;
int stpb;
int starr;
//indicator
const int led = 13;
//auxiliary variables
int count, x = 0;
int pos, contador = 0;
int contadorattack = 750;
int val, poslast, contador2, contador3 = 0;
int timev = 100;
int wait, wait2, wait3 = 0;
byte R_1 = 0, M_1 = 0, L_1 = 0;
byte sensores;

void setup() {
  //TCCR2B = TCCR2B & B11111000 | B00000001;
  //set timer 2 divisor to     1 for PWM frequency of 31372.55 Hz

  //TCCR2B = TCCR2B & B11111000 | B00000010;
  //set timer 2 divisor to     8 for PWM frequency of  3921.16 Hz

  TCCR2B = TCCR2B & B11111000 | B00000011;
  //set timer 2 divisor to    32 for PWM frequency of   980.39 Hz

  //TCCR2B = TCCR2B & B11111000 | B00000100;
  //set timer 2 divisor to    64 for PWM frequency of   490.20 Hz (The DEFAULT)

  //TCCR2B = TCCR2B & B11111000 | B00000101;
  //set timer 2 divisor to   128 for PWM frequency of   245.10 Hz

  //TCCR2B = TCCR2B & B11111000 | B00000110;
  //set timer 2 divisor to   256 for PWM frequency of   122.55 Hz

  //TCCR2B = TCCR2B & B11111000 | B00000111;
  //set timer 2 divisor to  1024 for PWM frequency of    30.64 Hz

  pinMode(in1, OUTPUT);
  pinMode(a1, OUTPUT);
  pinMode(a2, OUTPUT);
  pinMode(in2, OUTPUT);
  pinMode(b1, OUTPUT);
  pinMode(b2, OUTPUT);
  pinMode(sr, INPUT);
  pinMode(sm, INPUT);
  pinMode(sl, INPUT);
  pinMode(sf, INPUT);
  pinMode(pb, INPUT_PULLUP);
  pinMode(arr, INPUT);
  pinMode(led, OUTPUT);
  FastLED.addLeds<WS2812, DATA_PIN, RGB>(leds, NUM_LEDS);
  leds[0].setRGB(0, 0, 0);
  leds[1].setRGB(0, 0, 0);
}

void loop() {
  starr = digitalRead(arr);
  while (starr == LOW) {
    starr = digitalRead(arr);
    stpb = digitalRead(pb);
    if (stpb == LOW) {
      digitalWrite(led, HIGH);
      count = count + 1;
      delay(300);
      digitalWrite(led, LOW);
    }
  }

  while (starr == HIGH) {
      starr = digitalRead(arr);
      floor_move();
      if (starr == LOW) {
        count = 0;
        x = 0;
        break;
      }
  }
  stopB();
  digitalWrite(led, LOW);
  leds[0] = CRGB::Black;
  leds[1] = CRGB::Black;
  FastLED.show();
}

void floor_move() {
  stsf = analogRead(sf);
  if (stsf <= 60) {
    move();
  } else {
    conditions(count);
  }
}

void conditions(int countc) {
  switch (countc) {
    case 1:
      one();
      break;
    default:
      atacar();
      break;
  }
}

void read() {
  stsr = digitalRead(sr);
  stsm = digitalRead(sm);
  stsl = digitalRead(sl);

  if (stsr == 1) { R_1 = 0B00000001; }  //right sensor
  else {
    R_1 = 0B00000000;
  }
  if (stsm == 1) { M_1 = 0B00000010; }  //mid sensor
  else {
    M_1 = 0B00000000;
  }
  if (stsl == 1) { L_1 = 0B00000100; }  //left sensor
  else {
    L_1 = 0B00000000;
  }

  sensores = R_1 + M_1 + L_1;

  switch (sensores) {
    case 0B00000001:  //right
      pos = 100;
      leds[0] = CHSV(205, 255, 80);
      leds[1] = CHSV(205, 255, 80);
      FastLED.show();
      break;
    case 0B00000011:
      pos = 100;
      leds[0] = CHSV(125, 255, 80);
      leds[1] = CHSV(125, 255, 80);
      FastLED.show();
      break;
    case 0B00000100:  //left
      pos = 200;
      leds[0] = CHSV(55, 255, 80);
      leds[1] = CHSV(55, 255, 80);
      FastLED.show();
      break;
    case 0B00000110:
      pos = 200;
      leds[0] = CHSV(55, 255, 80);
      leds[1] = CHSV(55, 255, 80);
      FastLED.show();
      break;
    case 0B00000010:  //mid
      pos = 300;
      leds[0] = CHSV(125, 255, 80);
      leds[1] = CHSV(125, 255, 80);
      FastLED.show();
      break;
    case 0B00000111:
      pos = 300;
      leds[0] = CHSV(125, 255, 80);
      leds[1] = CHSV(125, 255, 80);
      FastLED.show();
      break;
    case 0B00000101:
      pos = 300;
      leds[0] = CHSV(125, 255, 80);
      leds[1] = CHSV(125, 255, 80);
      FastLED.show();
      break;
    default:
      pos = 0;
      leds[0] = CRGB::Black;
      leds[1] = CRGB::Black;
      FastLED.show();
      break;
  }
  if (poslast == 100 && pos == 0) {
    pos = 100;
    contador2 = contador2 + 1;
  }
  if (poslast == 200 && pos == 0) {
    pos = 200;
    contador3 = contador3 + 1;
  }
  if (contador2 == timev) {
    pos = 0;
    contador3 = 0;
    contador2 = 0;
  }
  if (contador3 == timev) {
    pos = 0;
    contador3 = 0;
    contador2 = 0;
  }
  poslast = pos;
  return pos;
}

void atacar() {
  read();
  switch (pos) {
    case 100:
      right(100, 100);
      contador = 0;
      break;
    case 200:
      left(100, 100);
      contador = 0;
      break;
    case 300:
      contador = contador + 1;
      if (contador >= contadorattack) {
        forwards(155, 155);
      } else {
        forwards(35, 35);
      }
      break;
    default:
      forwards(50, 50);
      contador = 0;
      break;
  }
}

void one() {
  while (x < 1) {
    right(205, 205);
    delay(60);
    x = x + 1;
  }
  atacar();
}

//---------------------------------------

void move() {
  backwards(205, 205);
  delay(100);
  right(205, 205);
  delay(100);
}

void backwards(int pwml, int pwmr) {
  analogWrite(in1, pwmr);
  digitalWrite(a1, LOW);
  digitalWrite(a2, HIGH);
  //-----------------------
  analogWrite(in2, pwml);
  digitalWrite(b1, LOW);
  digitalWrite(b2, HIGH);
}

void forwards(int pwml, int pwmr) {
  analogWrite(in1, pwmr);
  digitalWrite(a1, HIGH);
  digitalWrite(a2, LOW);
  //-----------------------
  analogWrite(in2, pwml);
  digitalWrite(b1, HIGH);
  digitalWrite(b2, LOW);
}

void right(int pwml, int pwmr) {
  analogWrite(in1, pwmr);  //RIGHT
  digitalWrite(a1, LOW);
  digitalWrite(a2, HIGH);
  //-----------------------
  analogWrite(in2, pwml);  //LEFT
  digitalWrite(b1, HIGH);
  digitalWrite(b2, LOW);
}

void left(int pwml, int pwmr) {
  analogWrite(in1, pwmr);  //left
  digitalWrite(a1, HIGH);
  digitalWrite(a2, LOW);
  //-----------------------
  analogWrite(in2, pwml);  //right
  digitalWrite(b1, LOW);
  digitalWrite(b2, HIGH);
}

void stop() {
  analogWrite(in1, 255);  //right
  digitalWrite(a1, LOW);
  digitalWrite(a2, LOW);
  //-----------------------
  analogWrite(in2, 255);  //left
  digitalWrite(b1, LOW);
  digitalWrite(b2, LOW);
}

void stopB() {
  analogWrite(in1, 0);  //right
  digitalWrite(a1, HIGH);
  digitalWrite(a2, HIGH);
  //-----------------------
  analogWrite(in2, 0);  //left
  digitalWrite(b1, HIGH);
  digitalWrite(b2, HIGH);
}

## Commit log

2024-12-14 Second commit
    [base_microsumo_pro.SLDPRT]
2024-12-14 Ultima 14-12
    [base_microsumo_pro.SLDPRT]
